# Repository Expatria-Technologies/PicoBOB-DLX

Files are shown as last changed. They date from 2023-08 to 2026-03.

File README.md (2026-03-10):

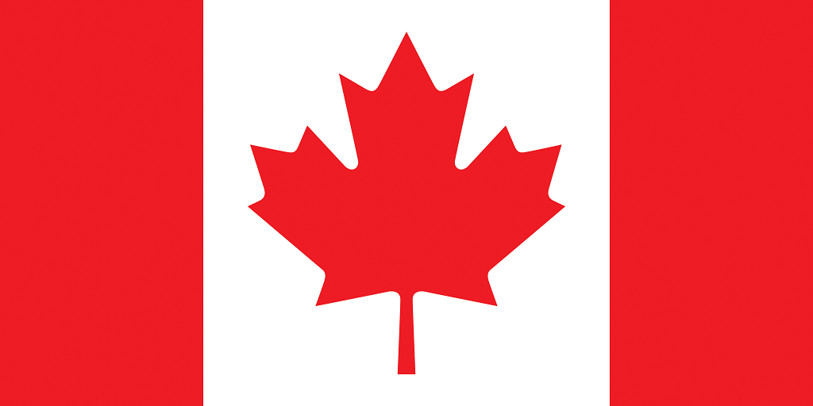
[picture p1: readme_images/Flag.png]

### Canadian-designed open source hardware. For everyone.

# PicoBOB-DLX for GRBLHAL and LinuxCNC

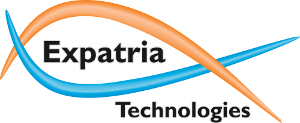
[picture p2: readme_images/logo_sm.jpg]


Expatria Technologies PicoBOB-DLX GRBLHAL/LinuxCNC module

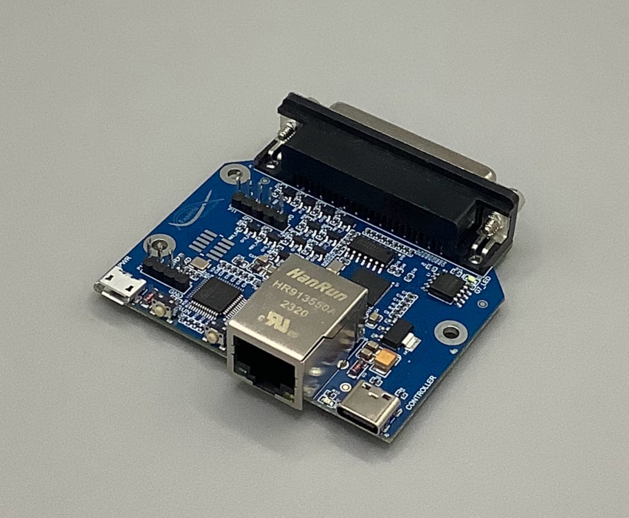
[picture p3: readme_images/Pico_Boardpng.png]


Currently available in our online store:

[https://expatria.myshopify.com/products/picobob-dlx](https://expatria.myshopify.com/products/picobob-dlx)

Please consider buying a board to support our open-source designs. 

An extended version of the original PicoBOB, the PicoBOB-DLX allows you to use either the MCU/Sender based GRBLHAL motion control system, or else it can act as a hardware step generator when connected to a LinuxCNC system over Ethernet.  It is intended to be simple and low cost.  It uses a Raspberry Pi RP2040 MCU and the widely available 5 axis Mach3 breakout board.  It can also be used with the Gecko G540 as well as other devices that use a DB25 parallel port interface.  The complete BOM and fabrications files are in the CAM_OUTPUTS folder for upload.  The design is free to use by all parties, including commercial parties, under the CERN-OHL-S V2 license.  It is our hope that the community finds the design useful and that it may be carried forward to help advance the PrintNC and broader CNC hobby community.

The PicoBOB-DLX closely tracks the features of the Mach3/LinuxCNC BOB:

1) Up to 5 axes of step/direction control.
3) 10A Spindle relay control.
4) 0-10V analog spindle speed control.
5) 5 general purpose inputs
6) One general purpose output.

In addition, it has headers for the Expatria Jog2K real-time control pendant: 

https://github.com/Expatria-Technologies/RT_Jog_Controller

The DLX can be connected to a GRBLHAL host via Ethernet or USBC.  For LinuxCNC, the Ethernet connection is used with the Remora etherent component and the DLX acts as a hardware step generator to mitigate latency demands.

The current work-in-progress version of the Remora RP2040-W5500 firmware is posted here:  
https://github.com/Expatria-Technologies/Remora-RP2040-W5500

The most current version of the GRBLHAL RP2040 driver is posted here:  
https://github.com/Expatria-Technologies/RP2040

The default GRBLHAL builds for the PicoBOB include the following features that are implemented in the RP2040 port of GRBLHAL:

1) Backlash Compensation.
2) Stress-free Autosquaring for the ganged axis
3) Ganged axis offsets to correct for offset homing switches
4) Step rates tested up to 180 KHz on 5 simultaneous axes.

In addition, the board has a USB micro connector for the 5V that is required for the BOB.  There are also pushbuttons for BOOT and RUN for easy programming using the RP2040's built-in UF2 bootloader.

## PicoBOB Overview

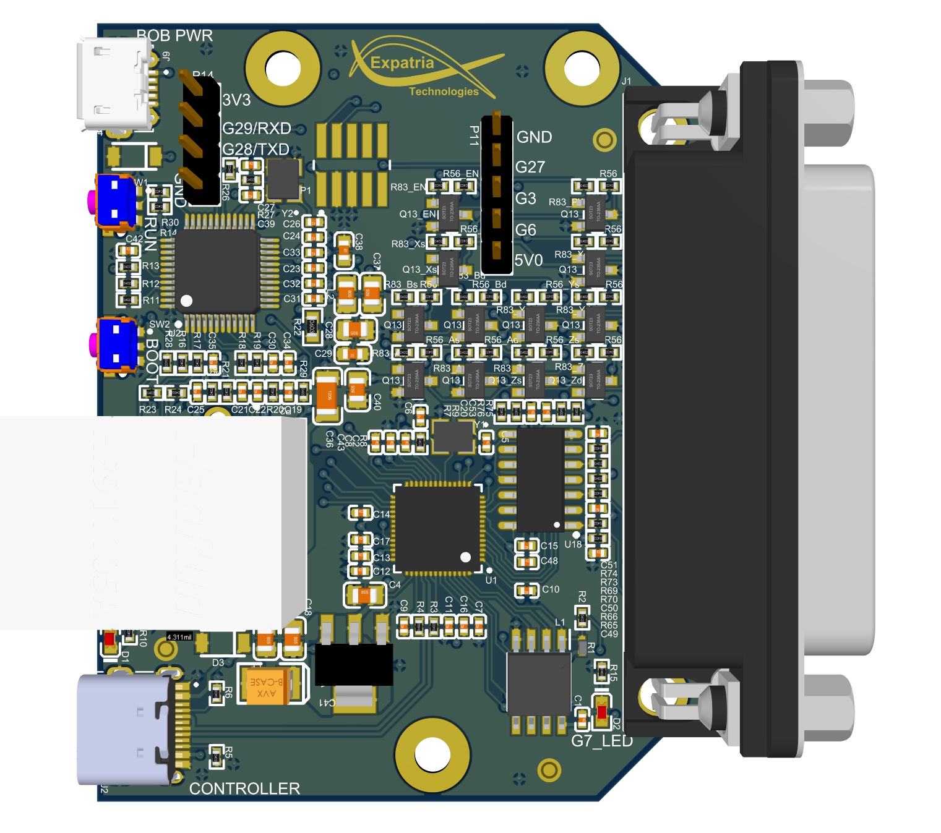
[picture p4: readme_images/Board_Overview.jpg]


Usage notes:

Communication with GRBLHAL is accomplished via the USBC or Ethernet connections on the PicoBOB (not connected in above images).  A short USB cable is used to provide the required 5V for the BOB.  In addition, the BOB requires an external 12-24V supply.

The Mach3 BOB shares the B axis direction signal with a spindle relay enable signal - only one can be used at a time.  Also on the PicoBOB, the stepper enable signal is modified in the GRBLHAL default map file so that it is used as the coolant output signal.  All of this is configurable by re-building the GRBLHAL firwmare.  In linuxcnc, the configuration is uploaded via tftp.

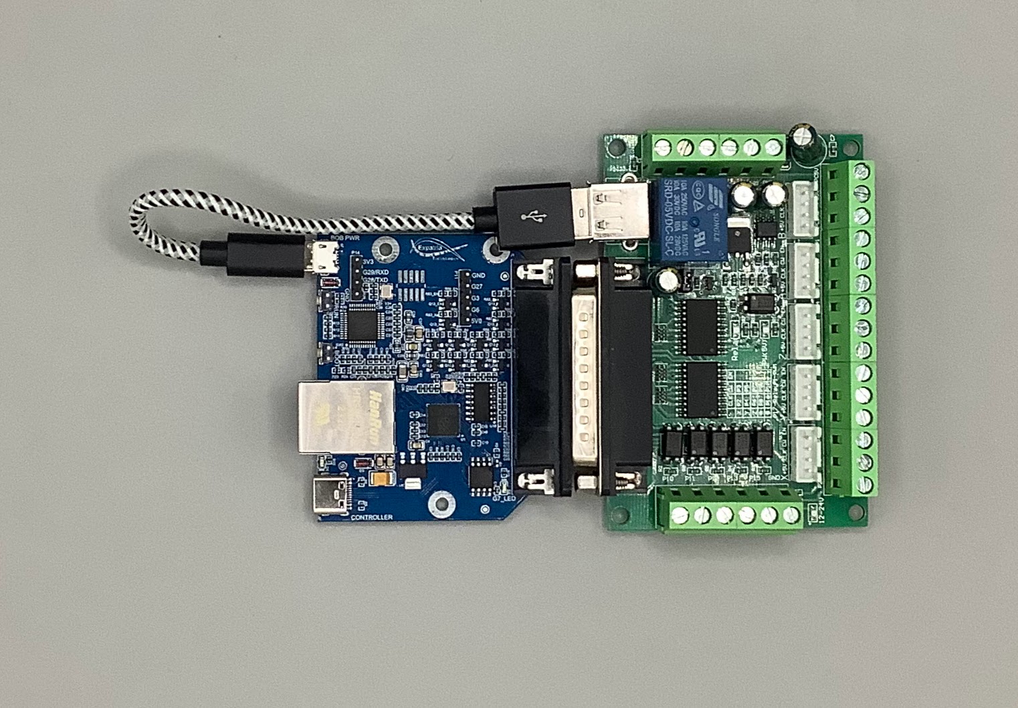
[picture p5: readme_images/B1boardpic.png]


Above shows the PicoBOB B1 connected to the Mach3/LinuxCNC parallel BOB.

YGANG pinout is as below:

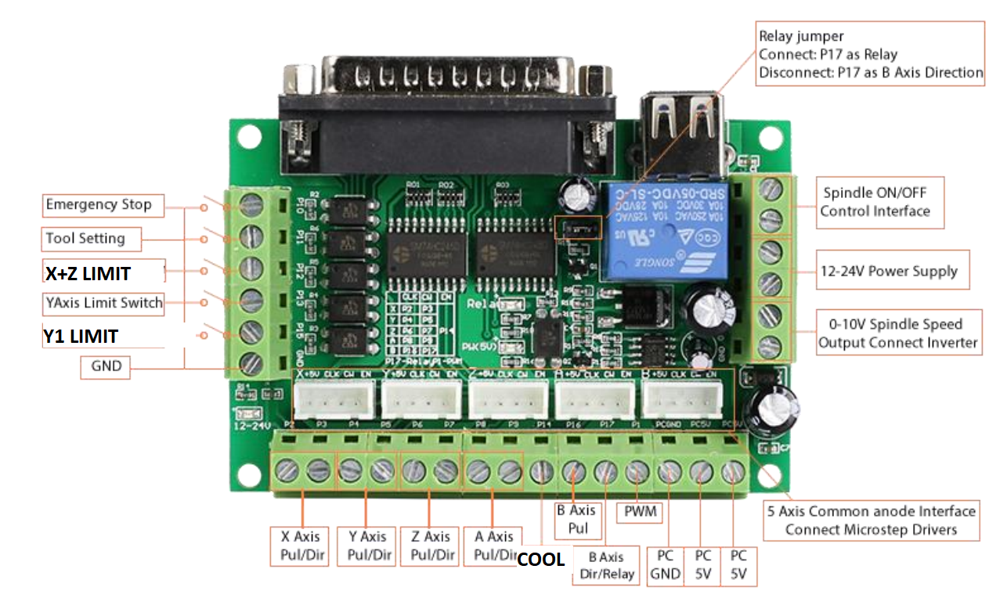
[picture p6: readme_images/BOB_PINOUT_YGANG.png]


## Gecko Drive G540 support Overview
By using a common "mini gender changer" the PicoBOB DLX can be adapted for use with a G540 4-AXIS Digital Step Drive.

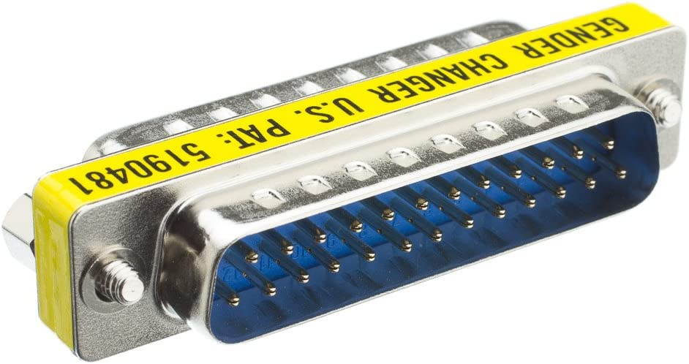
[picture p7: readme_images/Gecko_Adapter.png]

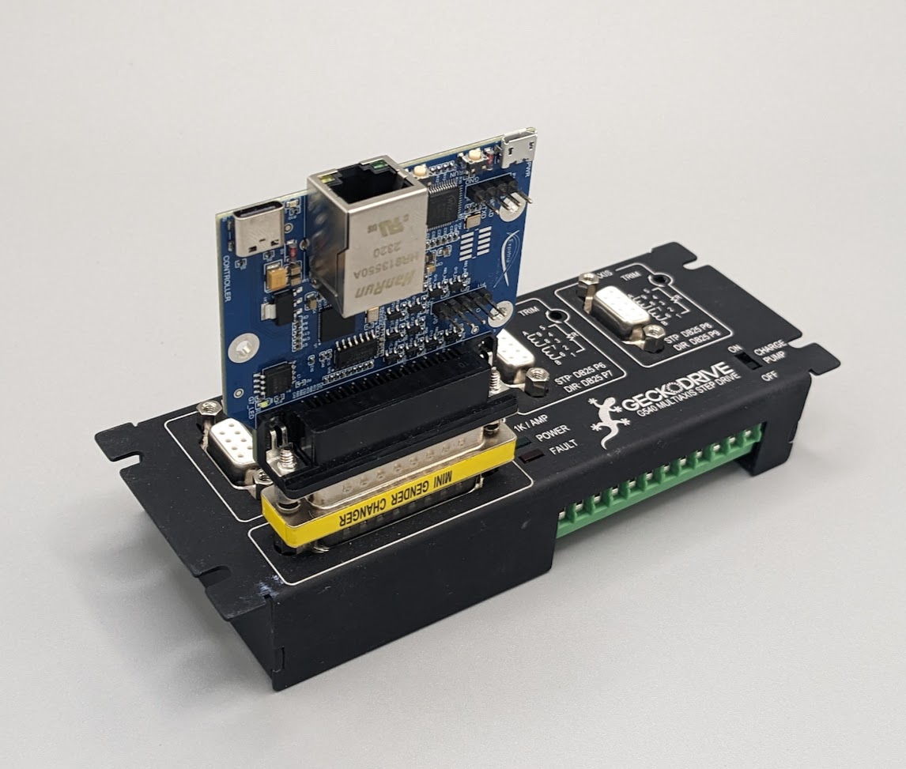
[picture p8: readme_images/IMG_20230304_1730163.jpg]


The updated GRBLHAL map file has the following pinout:

| DB25 Pin | G540 Function | GRBLHAL Function | RP2040 GPIO |
|---|---|---|---|
| Pin 1 | OUTPUT 2 | SPINDLE ENABLE | GPIO14 |
| Pin 2 | X STEP | X STEP | GPIO17 |
| Pin 3 | X DIR | X DIR | GPIO9 |
| Pin 4 | Y SETP | Y SETP | GPIO18 |
| Pin 5 | Y DIR | Y DIR | GPIO10 |
| Pin 6 | Z STEP | Z STEP | GPIO19 |
| Pin 7 | Z DIR | Z DIR | GPIO11 |
| Pin 8 | A STEP | A/M3 STEP | GPIO20 |
| Pin 9 | A DIR | A/M3 DIR | GPIO12 |
| Pin 10 | INPUT 1 | LIMIT XYZ | GPIO3 |
| Pin 11 | INPUT 2 | PROBE | GPIO4 |
| Pin 12 | INPUT 3 | LIMIT A/M3 | GPIO2 |
| Pin 13 | INPUT 4 | HOLD | GPIO1 |
| Pin 14 | VFD PWM | SPINDLE PWM | GPIO16 |
| Pin 15 | FAULT (INPUT 5) | HALT | GPIO5 |
| Pin 16 | CHARGE PUMP | N/A | GPIO21 |
| Pin 17 | OUTPUT 1 | COOLANT | GPIO13 |
| Pin 18-25| GND | | |

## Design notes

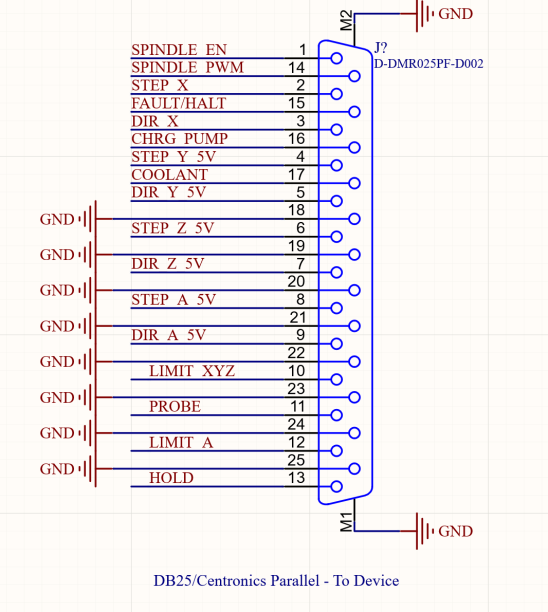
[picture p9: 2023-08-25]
readme_images/g540_pinout.png

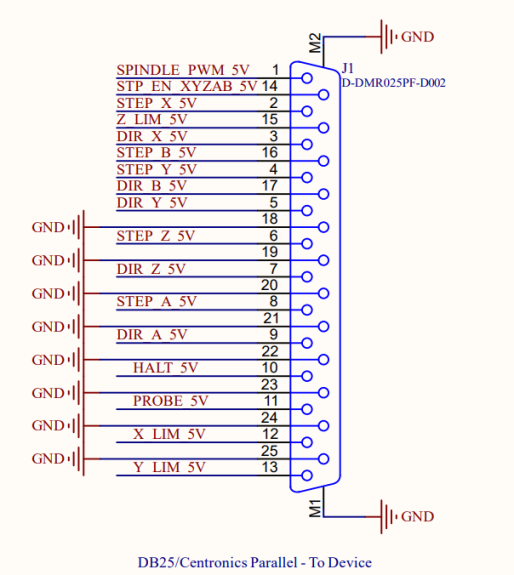
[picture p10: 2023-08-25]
readme_images/picoBOB_Pinout.png

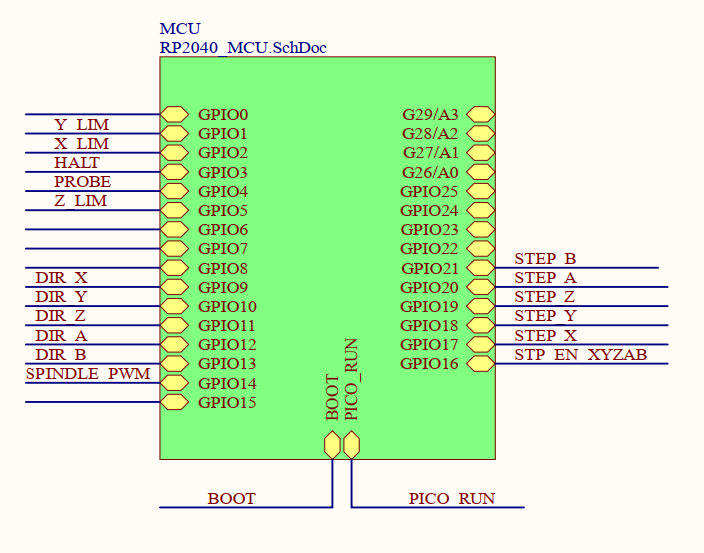
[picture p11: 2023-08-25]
readme_images/default_pinout.png

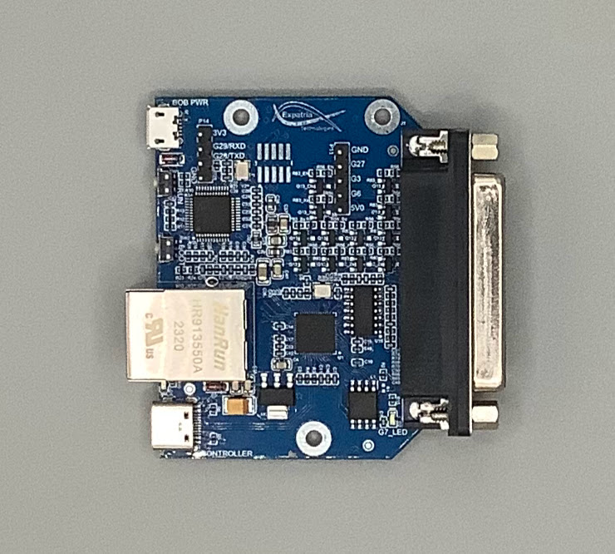
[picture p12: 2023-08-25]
readme_images/Pico_Top.png

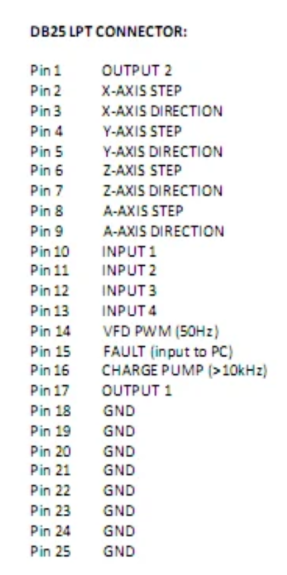
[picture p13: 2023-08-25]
readme_images/G540_DB25_ref.png

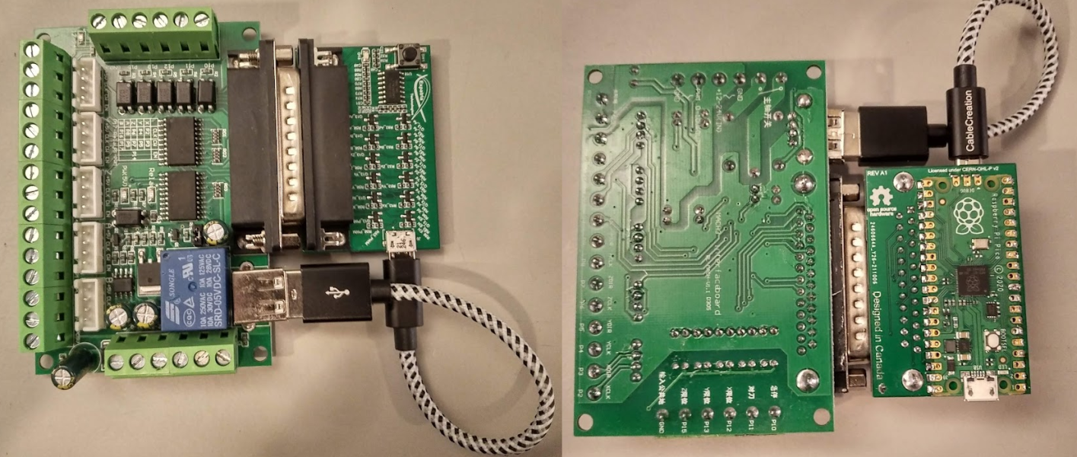
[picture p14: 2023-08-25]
readme_images/boardpics.png

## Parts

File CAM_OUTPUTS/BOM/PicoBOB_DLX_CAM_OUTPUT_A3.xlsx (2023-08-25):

Comment | Description | Designator | Footprint | SuppliersPartNumber | Quantity
100nF | Chip capacitors | C1, C7, C8, C11, C12, C13, C14, C15, C16, C17, C30, C31, C32, C33, C34, C35, C39 | 0402_C | C1525 | 17
4.7uF | Chip capacitor | C2, C23 | 0402_C | C23733 | 2
22uF | Chip capacitors | C3, C4, C18, C28, C37, C40 | 0805_C | C2922481 | 6
10pF | Chip capacitors | C5, C6, C26, C27 | 0402_C | C32949 | 4
1.0uF | Chip capacitor | C9, C10, C42, C43, C48 | 0402_C | C52923 | 5
10nF | Chip capacitors | C19, C20, C24, C49, C50, C51, C53 | 0402_C | C15195 | 7
6.8nF | Chip capacitors | C21, C22 | 0402_C | C1542 | 2
22nF | Chip capacitors | C25 | 0402_C | C1532 | 1
4.7uF | Chip capacitors | C29, C38 | 0603_C | C19666 | 2
1nF | Chip capacitors | C36 | 1206_C | C35216 | 1
100uF | Tantalum capacitor | C41 | CASE-B_3528 | C16133 | 1
0603 Green | LED | D1 | 0603_LED_S1 | C72043 | 1
0603 White | LED | D2 | 0603_LED_S1 | C2290 | 1
ZMM5V6 | 500mW - 0.1uA @ 1V 5.6V LL-34 Zener Diodes ROHS | D3, D4 | LL-34 | C8062 | 2
D-DMR025PF-D002 | Through Hole,P=2.77mm D-Sub Connectors ROHS | J1 | 618025231121 | C190083 | 1
TYPE-C-31-M-12 | USB Connectors 24 Receptacle 1 8.94*7.3mm RoHS | J2 | HRO_TYPE-C-31-M-12 | C165948 | 1
MICROXNJ | Micro USB | J9 | SHOUHAN_MICROXNJ | C404969 | 1
W25Q128JVSIQ_TR | Inductor | L1 | SOIC127P780X195-8N | C97521 | 1
220Ω @ 100MHz 1 2A | 220Ω @ 100MHz 1 2A 150mΩ 0805 Ferrite Beads ROHS | L2 | 0805_C | C139188 | 1
Magjack | HR911105A Ethernet Interface Arduino Platform Evaluation Expansion Board | P2 | HANRUN_HR911105A | C163507 | 1
Header 5 | Header, 5-Pin | P11 | HDR1X5 | C124379 | 1
Header 4 | Header, 4-Pin | P14 | HDR1X4 | C124378 | 1
MMBT5551 G1 | 三极管 | Q13_Ad, Q13_As, Q13_Bd, Q13_Bs, Q13_EN, Q13_PWM, Q13_Xd, Q13_Xs, Q13_Yd, Q13_Ys, Q13_Zd, Q13_Zs | SOT-23(SOT-23-3) | C2145 | 12
DNP | Resistor, ±5%, 0.05W | R1 | 0402 |  | 1
1KΩ ±1% | Chip resistor | R2 | 0402_R | C11702 | 1
22Ω ±1% | Chip resistor | R3, R4 | 0402_R | C25092 | 2
5.1KΩ ±1% | Chip resistor | R5, R6, R10 | 0402_R | C25905 | 3
100KΩ ±1% | Chip resistor | R7, R65, R69, R73, R75 | 0402_R | C25741 | 5
470Ω ±1% | Chip resistor | R8 | 0402_R | C25117 | 1
510Ω ±1% | Chip resistor | R9, R15, R66, R70, R74, R76 | 0402_R | C25123 | 6
10KΩ ±1% | Chip resistor | R11, R12, R13, R14 | 0402_R | C25744 | 4
33Ω ±1% | Chip resistor | R16, R17, R18, R19 | 0402_R | C25105 | 4
49.9Ω ±1% | Chip resistor | R20, R21, R23, R24 | 0402_R | C25120 | 4
12.4KΩ ±1% | Chip resistor | R22 | 0603_R | C22865 | 1
10Ω ±1% | Chip resistor | R25 | 0402_R | C25077 | 1
1MΩ ±1% | Chip resistor | R26 | 0402_R | C26083 | 1
0Ω ±1% | Chip resistor | R27 | 0402_R | C17168 | 1
330Ω ±1% | Chip resistor | R28, R29, R56_Ad, R56_As, R56_Bd, R56_Bs, R56_EN, R56_PWM, R56_Xd, R56_Xs, R56_Yd, R56_Ys, R56_Zd, R56_Zs | 0402_R | C25104 | 14
4.7KΩ ±1% | Chip resistor | R30 | 0402_R | C25900 | 1
2.2KΩ ±1% | Chip resistor | R83_Ad, R83_As, R83_Bd, R83_Bs, R83_EN, R83_PWM, R83_Xd, R83_Xs, R83_Yd, R83_Ys, R83_Zd, R83_Zs | 0402_R | C25879 | 12
SKRTLAE010 | Side Push Type, 250 V, -40 to 90 degC, 3-Pin SMD, RoHS, Tape and Reel | SW1, SW2 | ALPS-SKRTLAE010_V | C110293 | 2
RP2040 | RP2040 First MCU from RPI | U1 | RP2040 |  | 1
W5500 | Ethernet Controllers 2.97V ~ 3.63V 10/100 Base-T/TX PHY SPI LQFP-48_7x7x05P Ethernet ICs ROHS | U2 | LQFP-48_7x7x05P | C32843 | 1
74HC14D | 74系列逻辑芯片 | U18 | SOIC-14_150mil | C5605 | 1
AMS1117-3.3 | Vout=3.3V 1A 72dB@(120Hz) (LDO) | VR1 | SOT-223 | C6186 | 1
YSX321SL | Crystal or Oscillator | Y1 | YSX321SL | C9002 | 1
25.0 MHz | Crystal or Oscillator | Y2 | YSX321SL | C13740 | 1

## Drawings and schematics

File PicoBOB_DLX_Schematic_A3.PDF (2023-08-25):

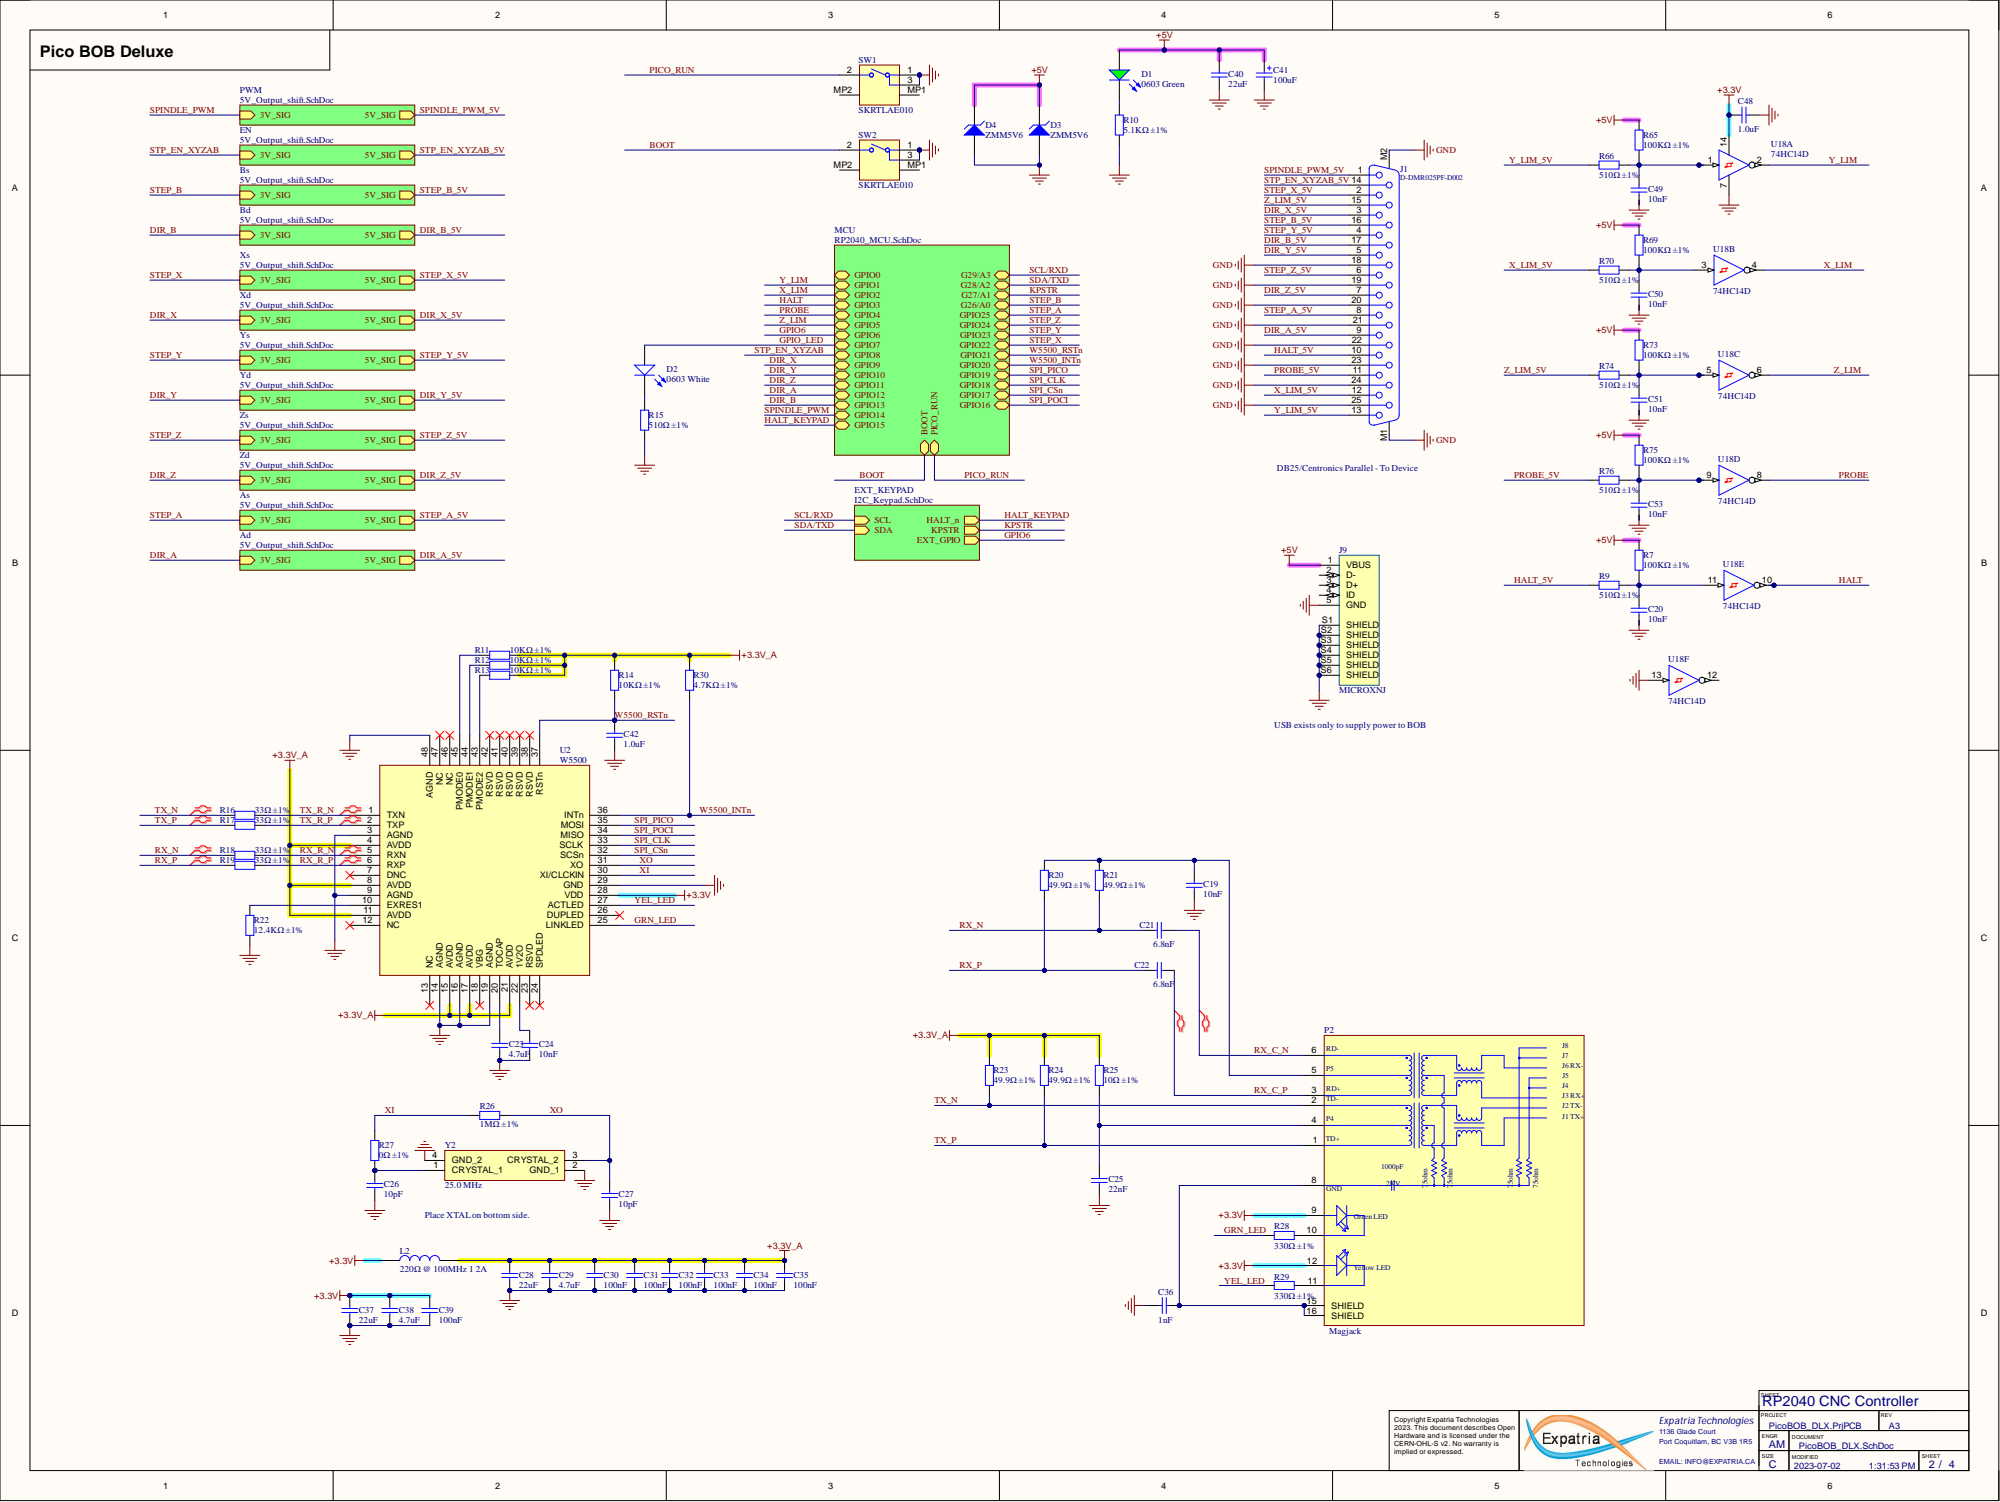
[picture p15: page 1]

R1 | 2 | 1 0 | K Ω ± 1 %
R1 | 3 | 1 0 | K Ω ± 1 %

Hardware a n d i s l i e s d u er th CERN-OHL-S v 2. No warra nty i m p or x pre . | | P OJE PicoBOB_DLX.Prj | R V A3

B Copyright Expatria Technologies 2023. This document describes Open

N G A | C U PicoBOB_DLX.Sc h D o c

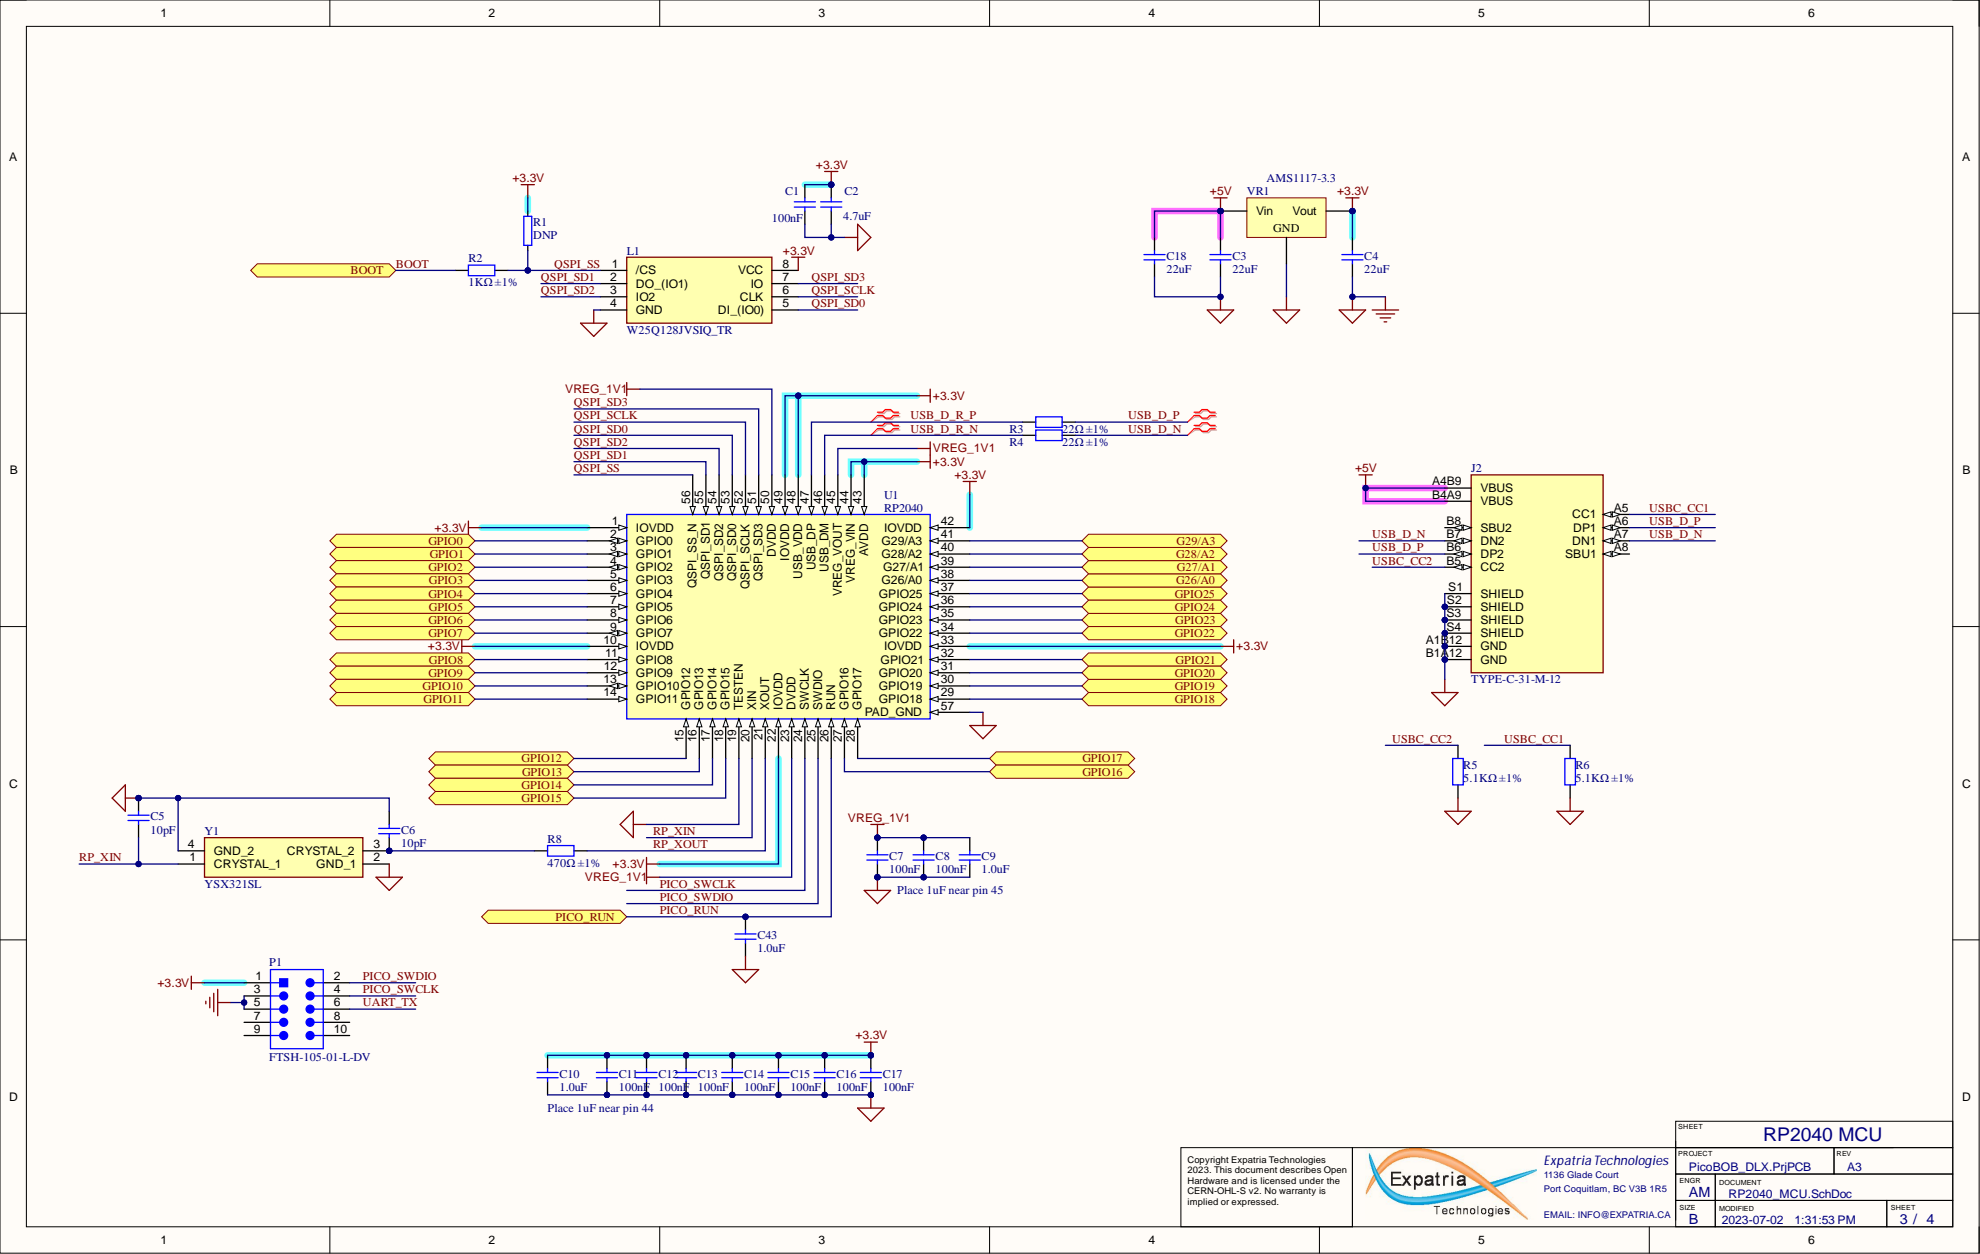
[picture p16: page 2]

QSPI_SD2
QSPI_SD1
QSPI_SS

Copyright Expatria Technologies 2023. This document describes Open Hardware and is licensed under the CERN-OHL-S v2. No warranty is implied or expressed. | | PROJECT PicoBOB_DLX.PrjPCB | REV

ENGR AM | DOCUMENT RP2040_MCU.SchDoc

SIZE B | MODIFIED 2023-07-02 1:31:53 PM | SHEET 3 / 4

EMAIL: INFO@EXPATRIA.CA

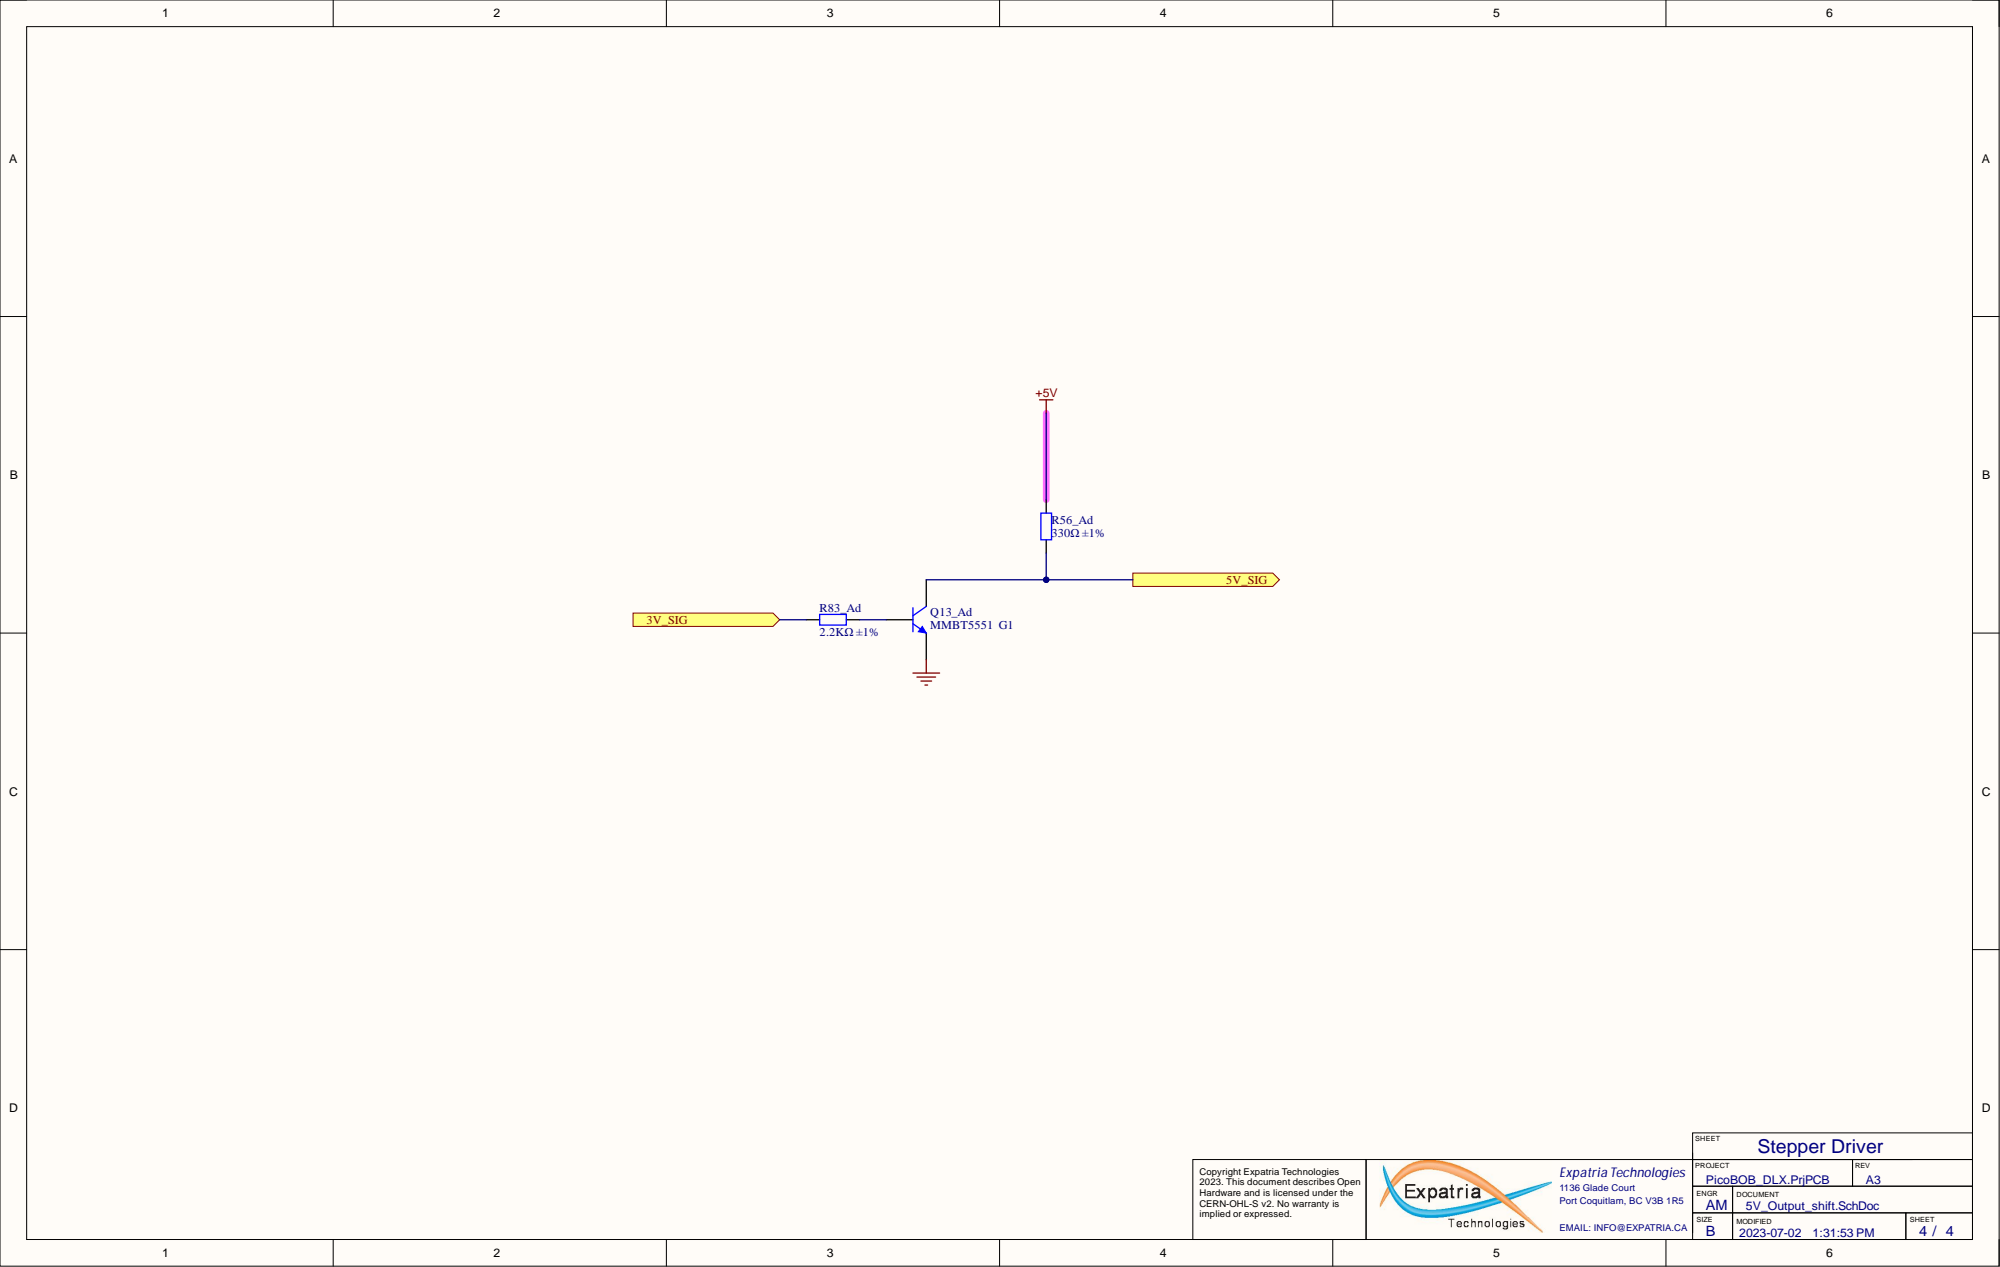
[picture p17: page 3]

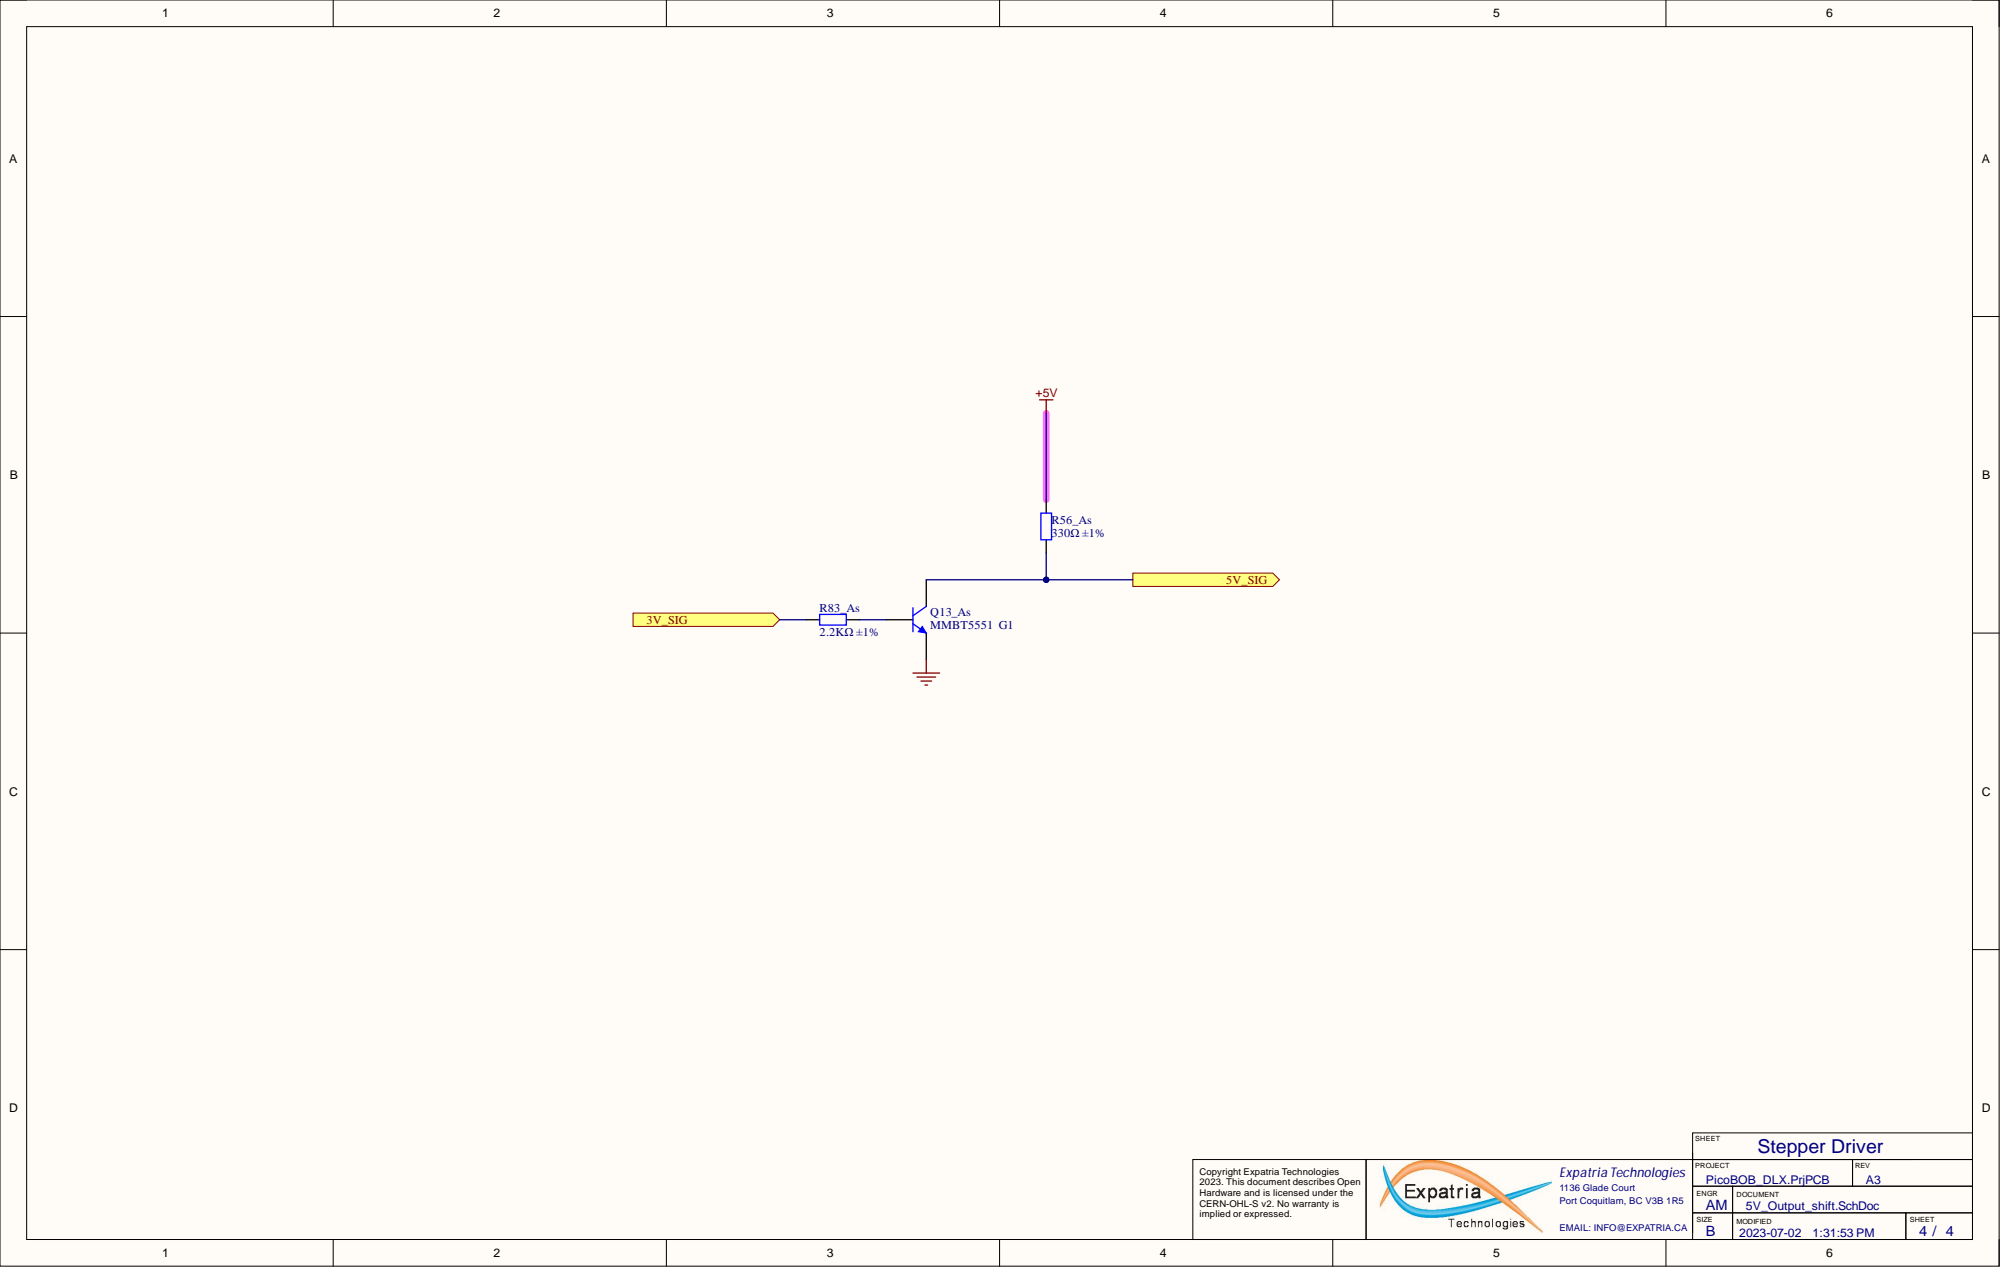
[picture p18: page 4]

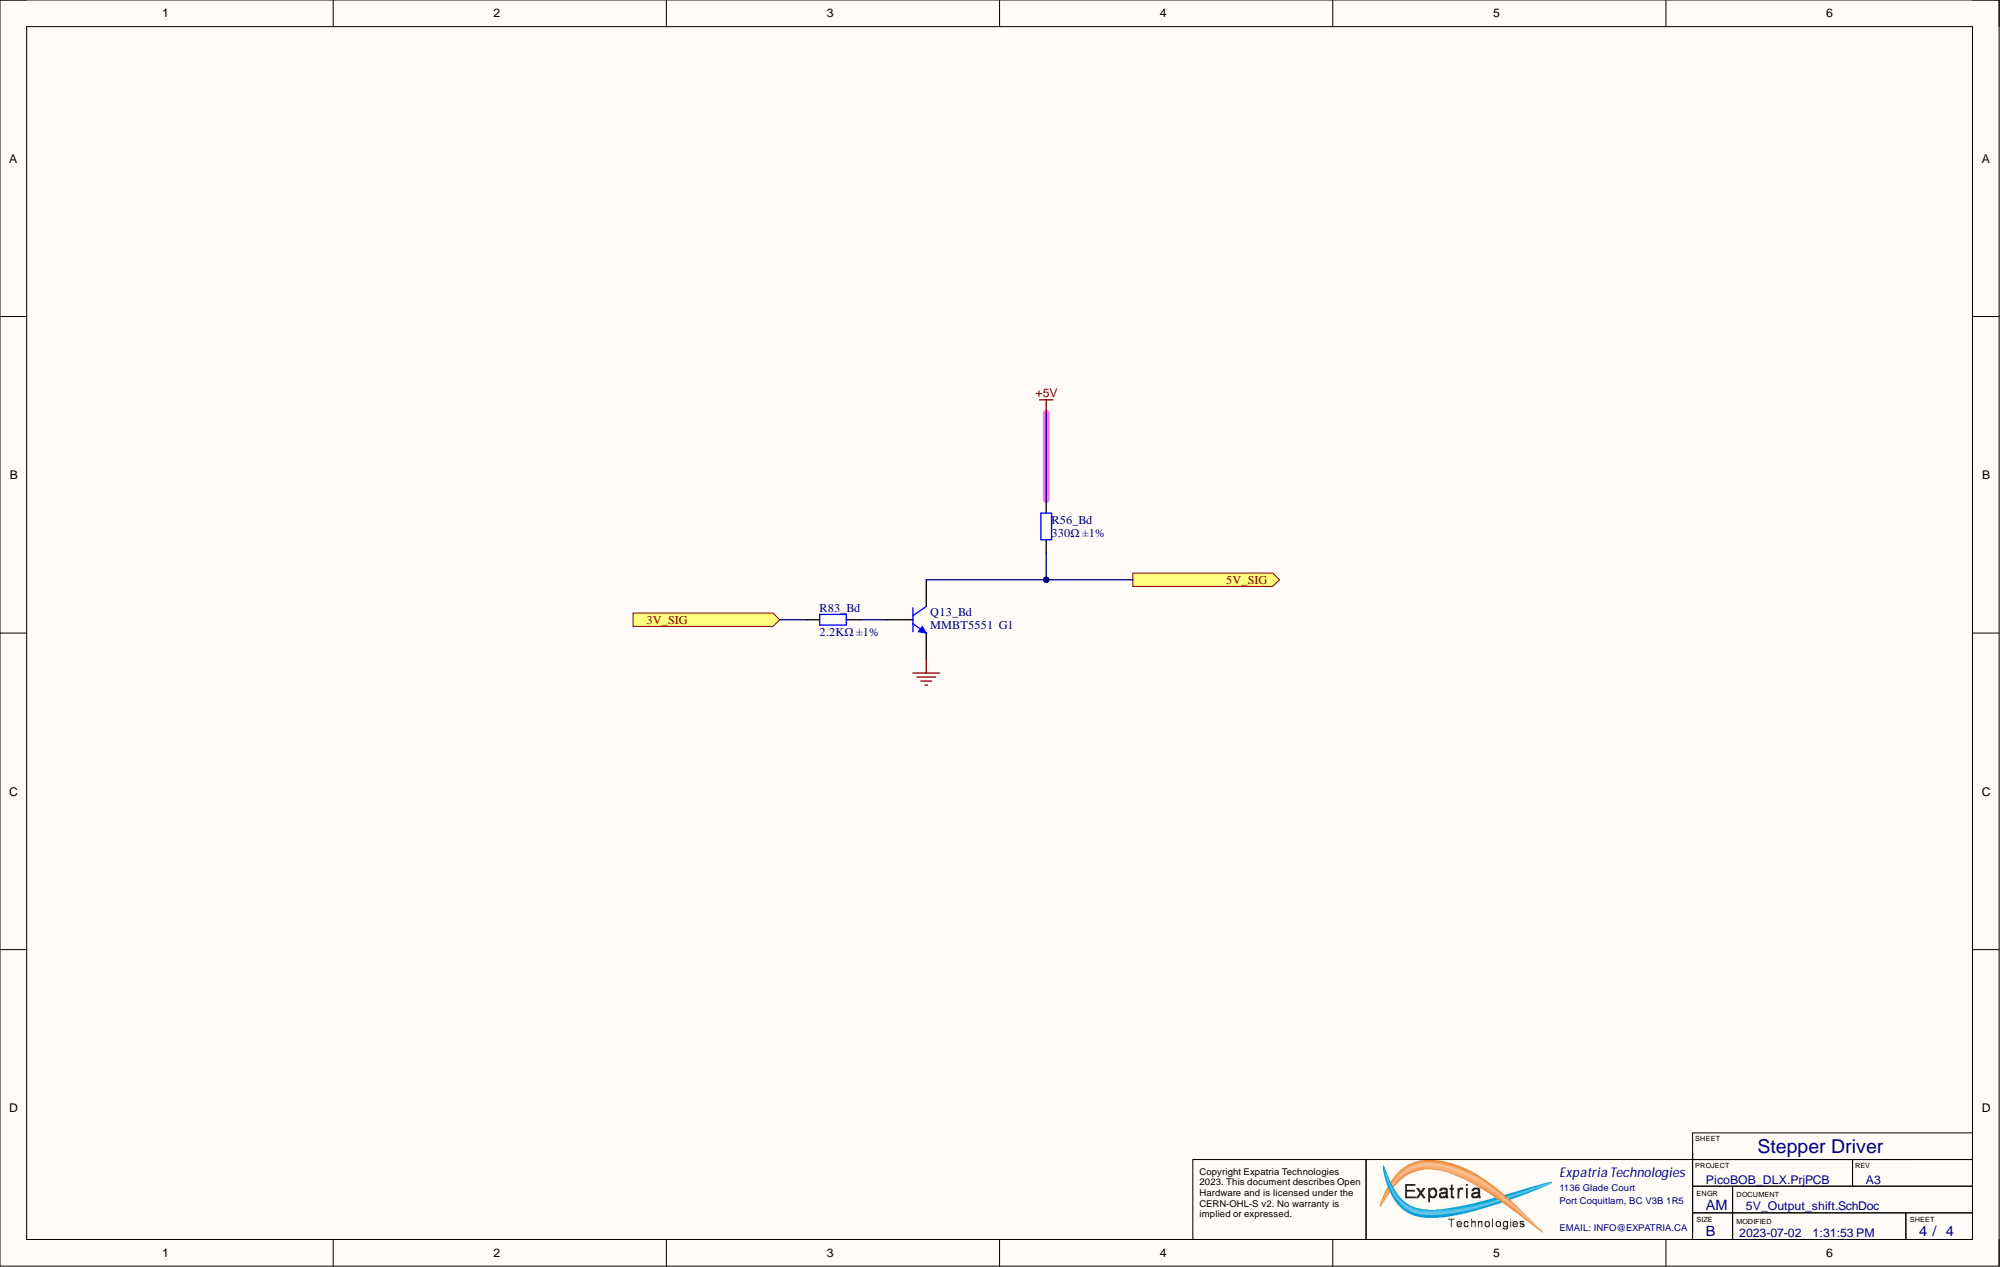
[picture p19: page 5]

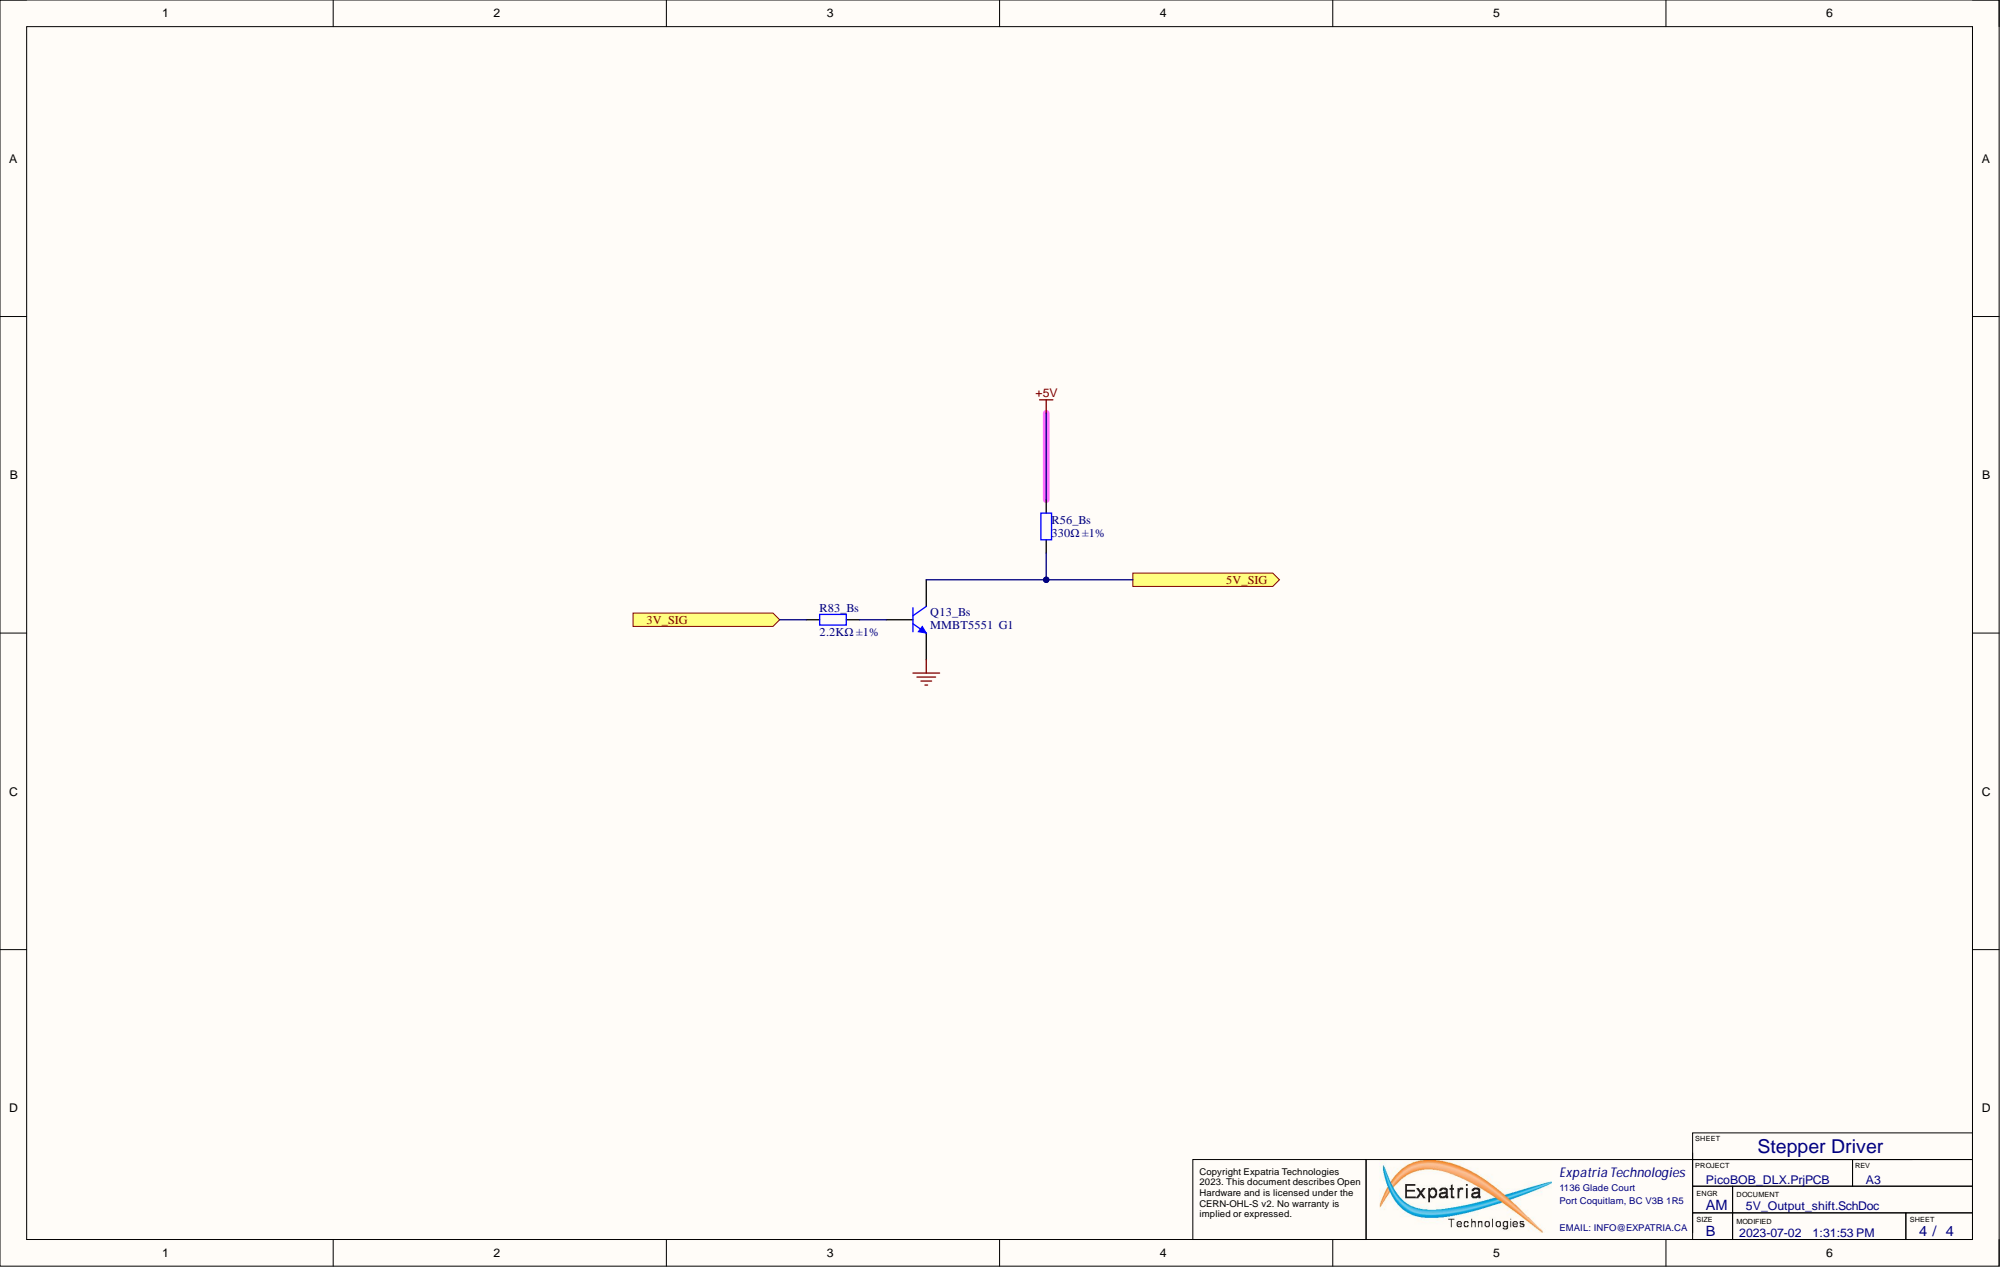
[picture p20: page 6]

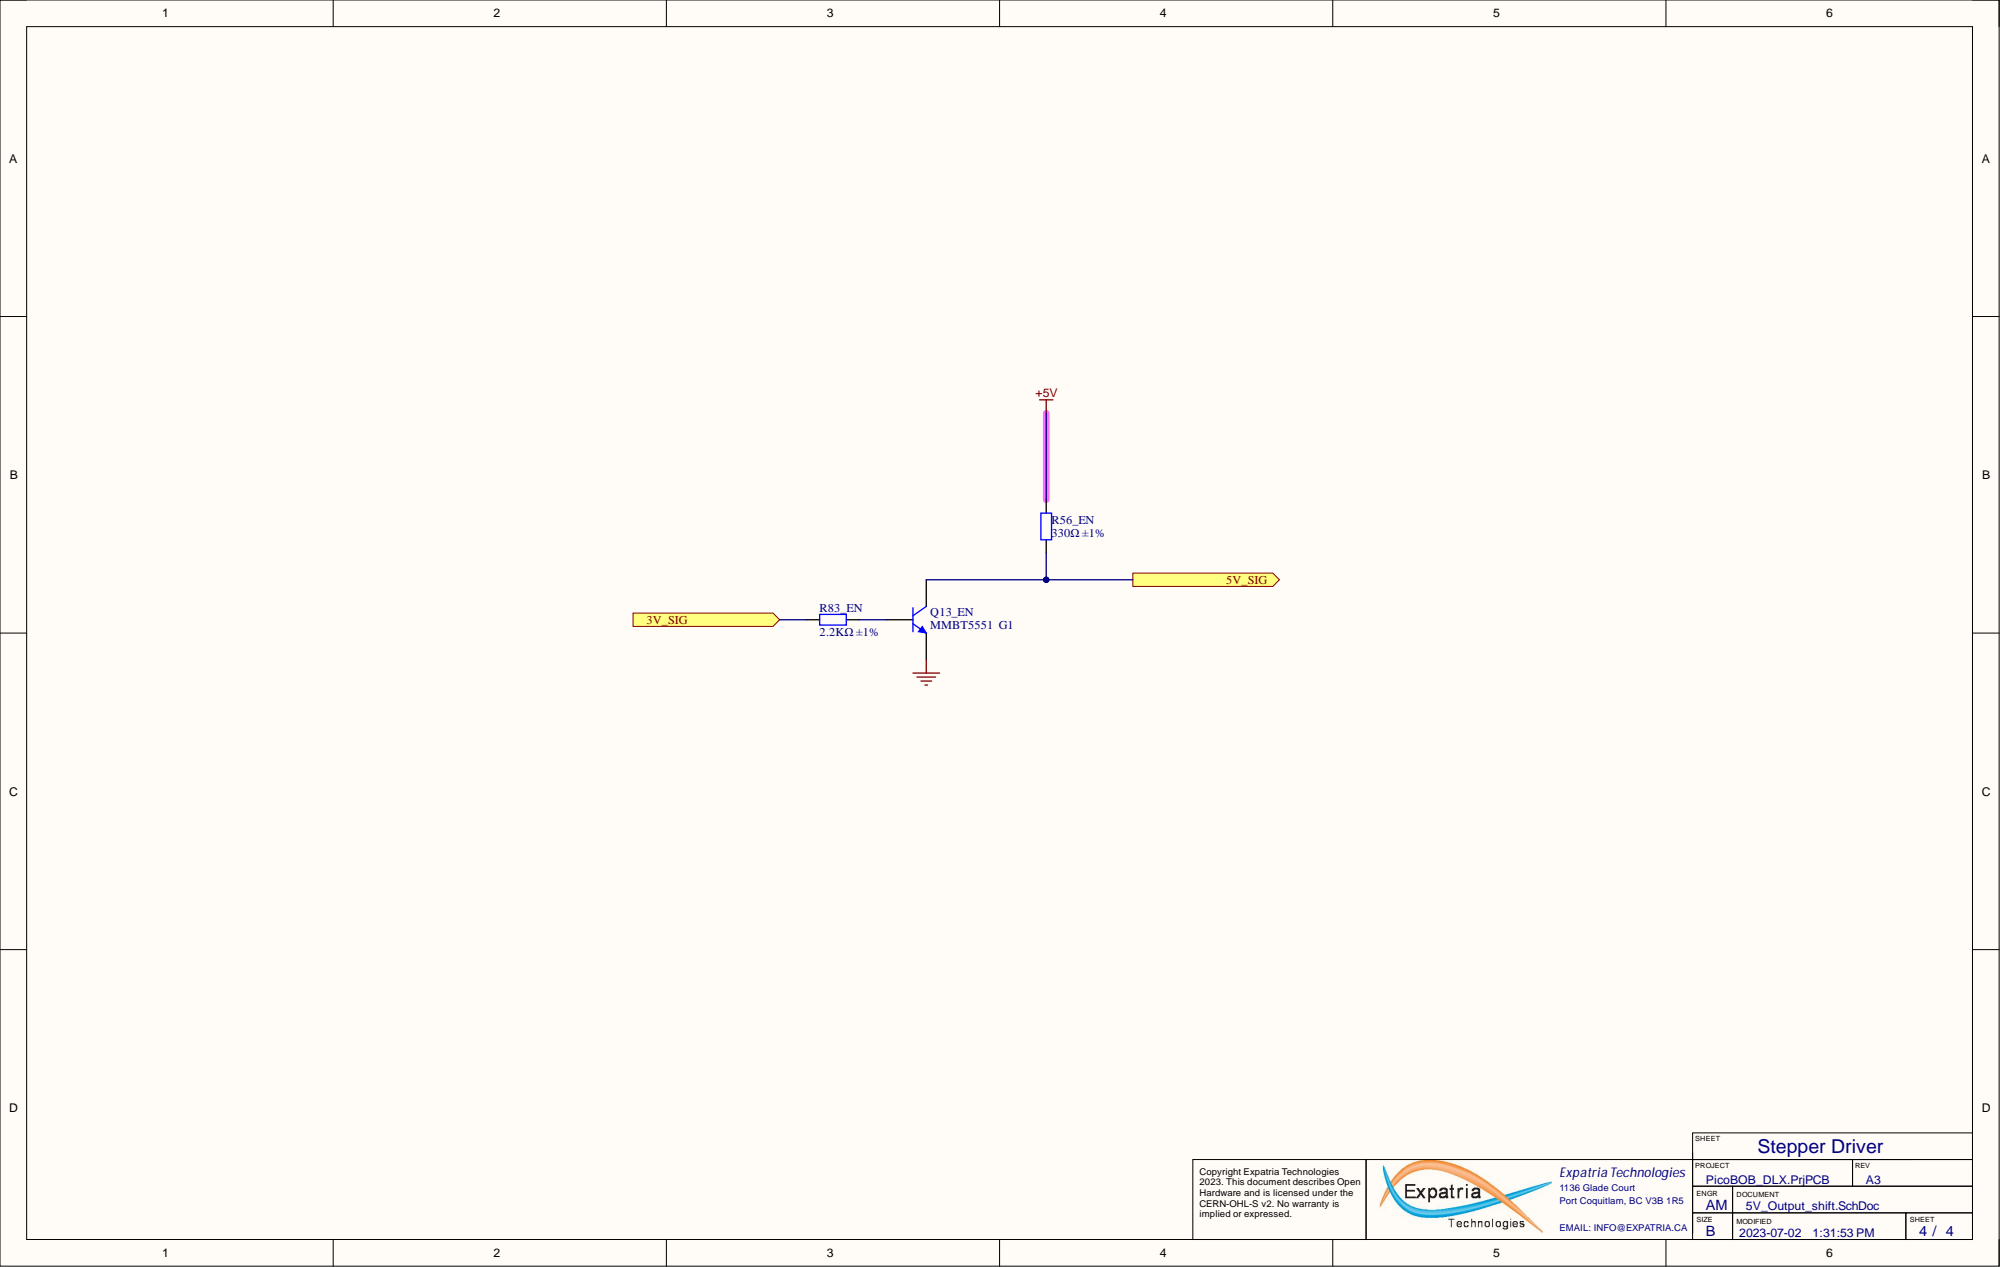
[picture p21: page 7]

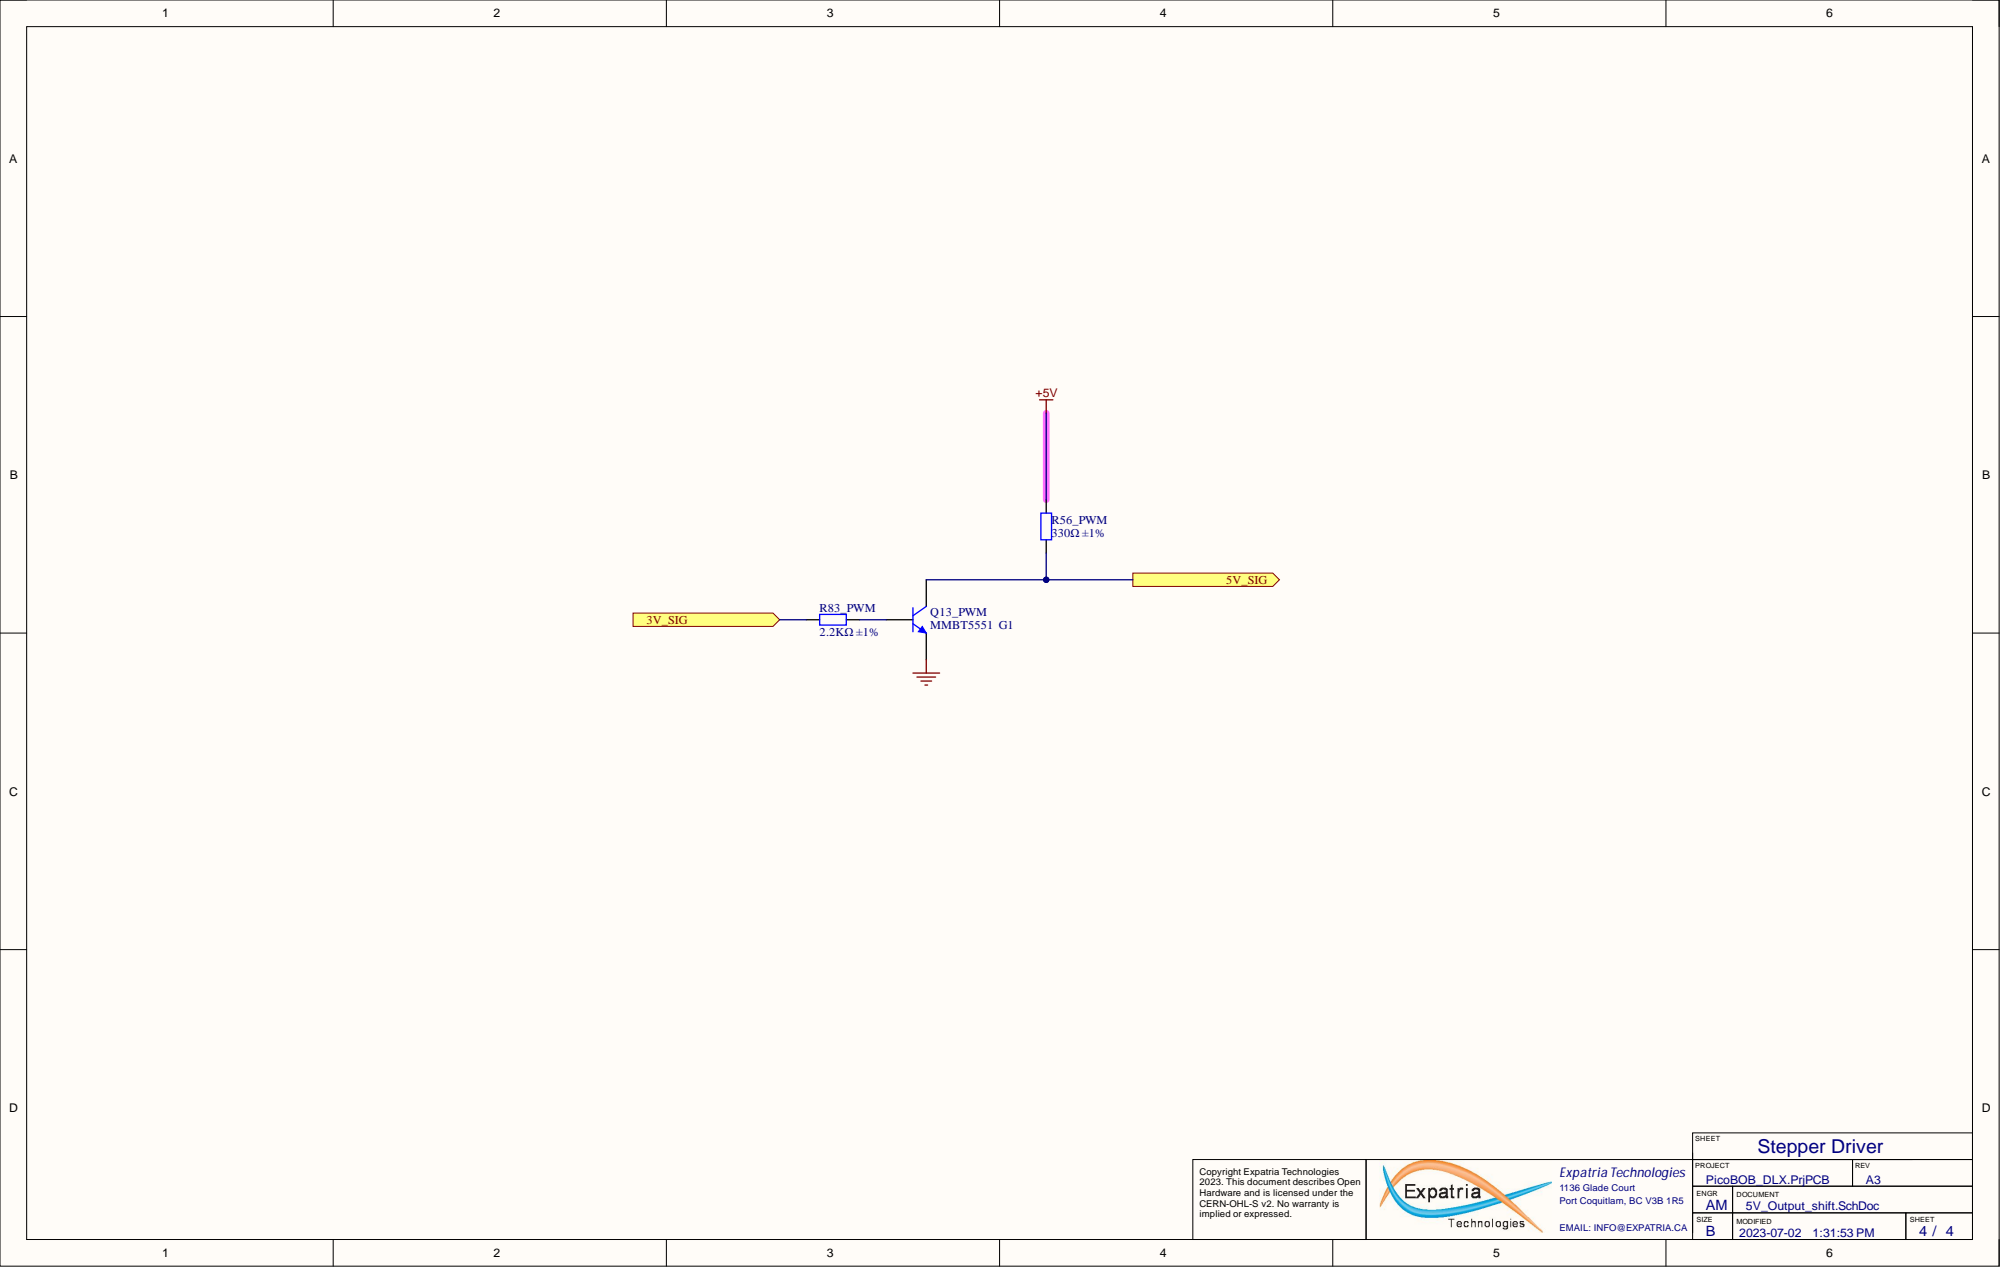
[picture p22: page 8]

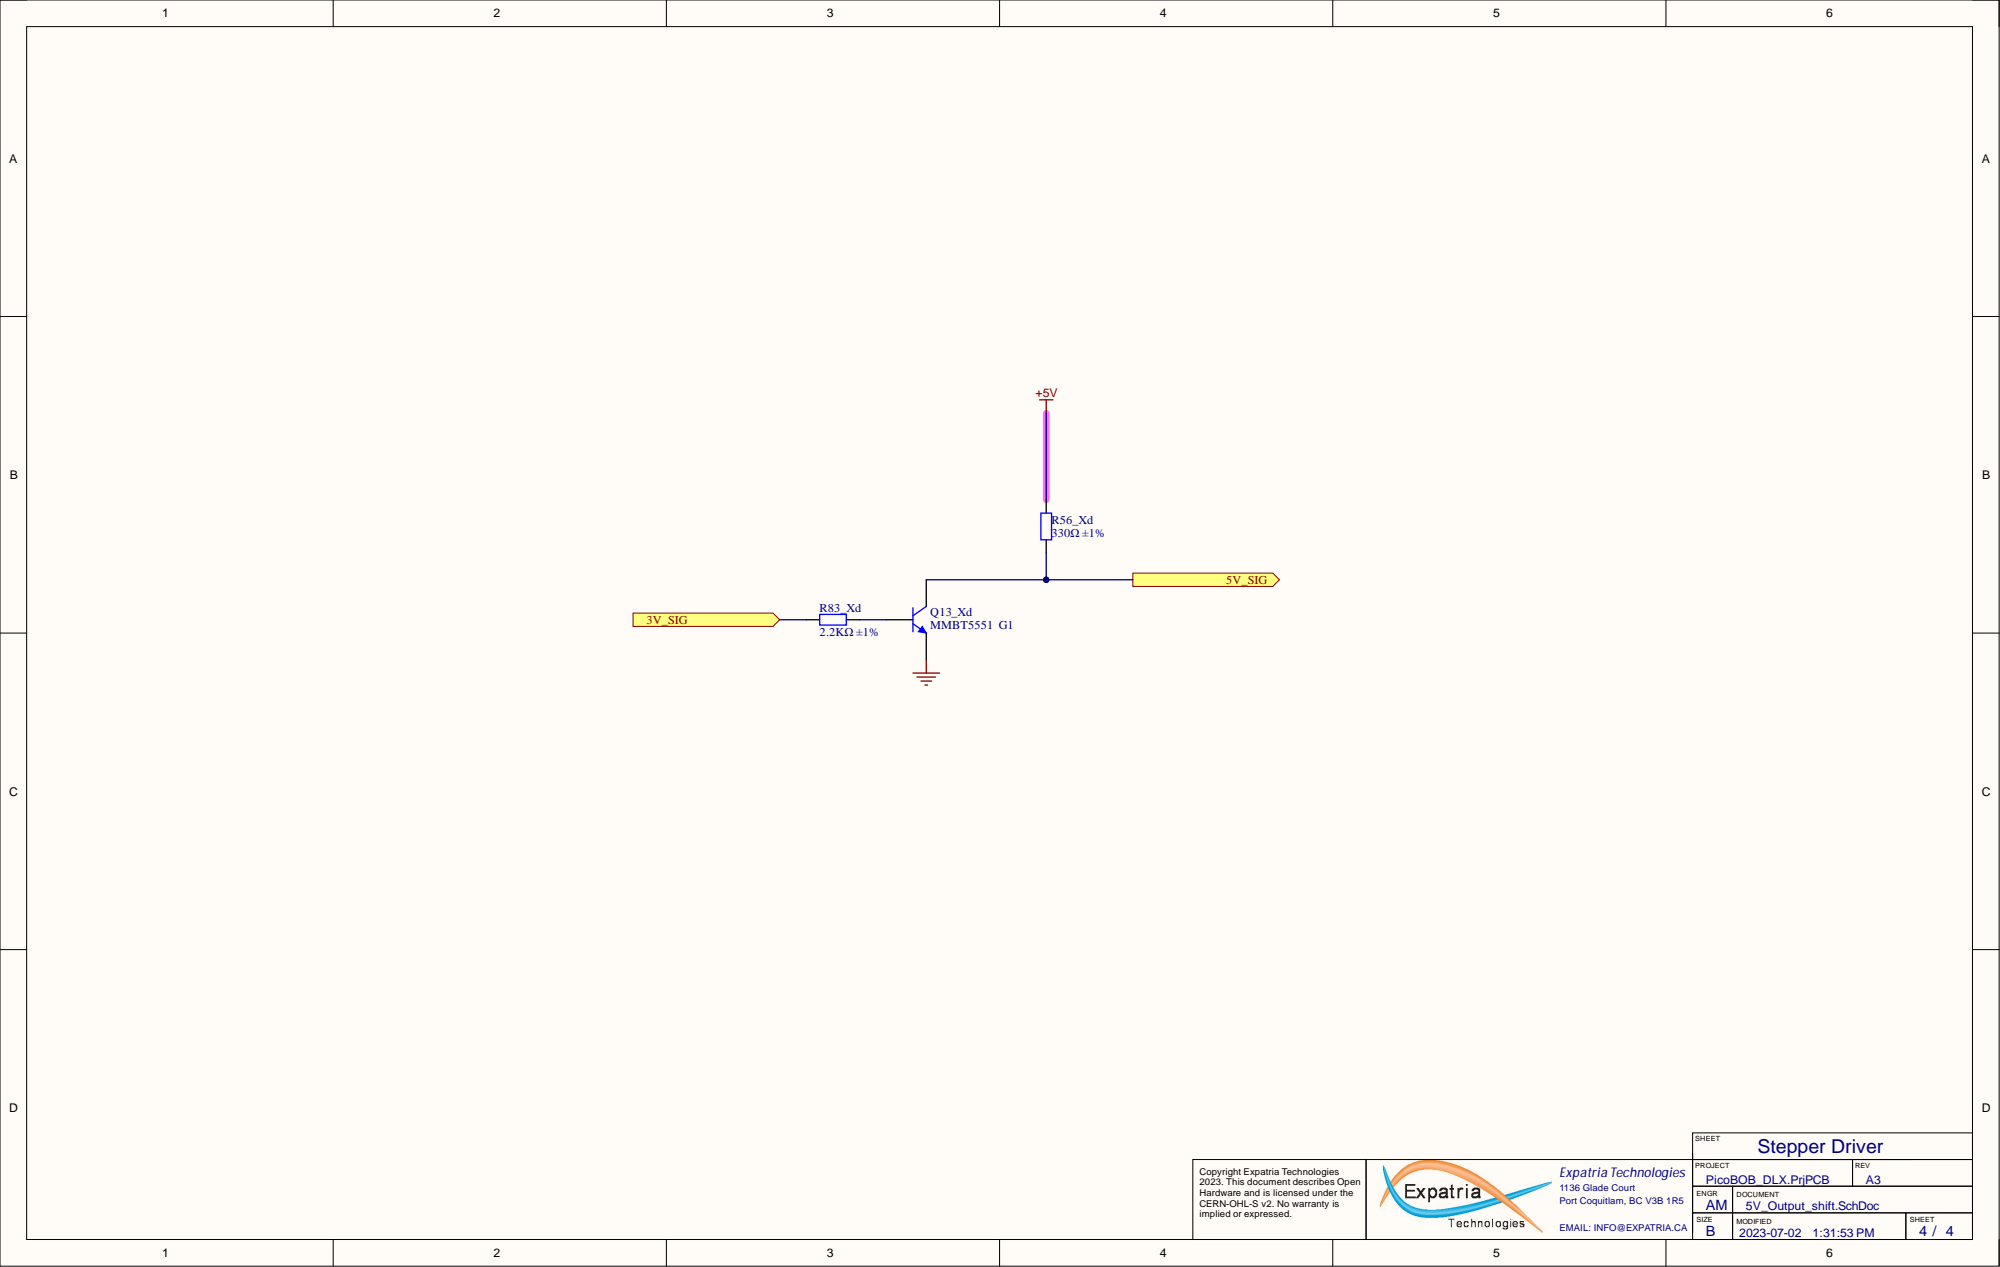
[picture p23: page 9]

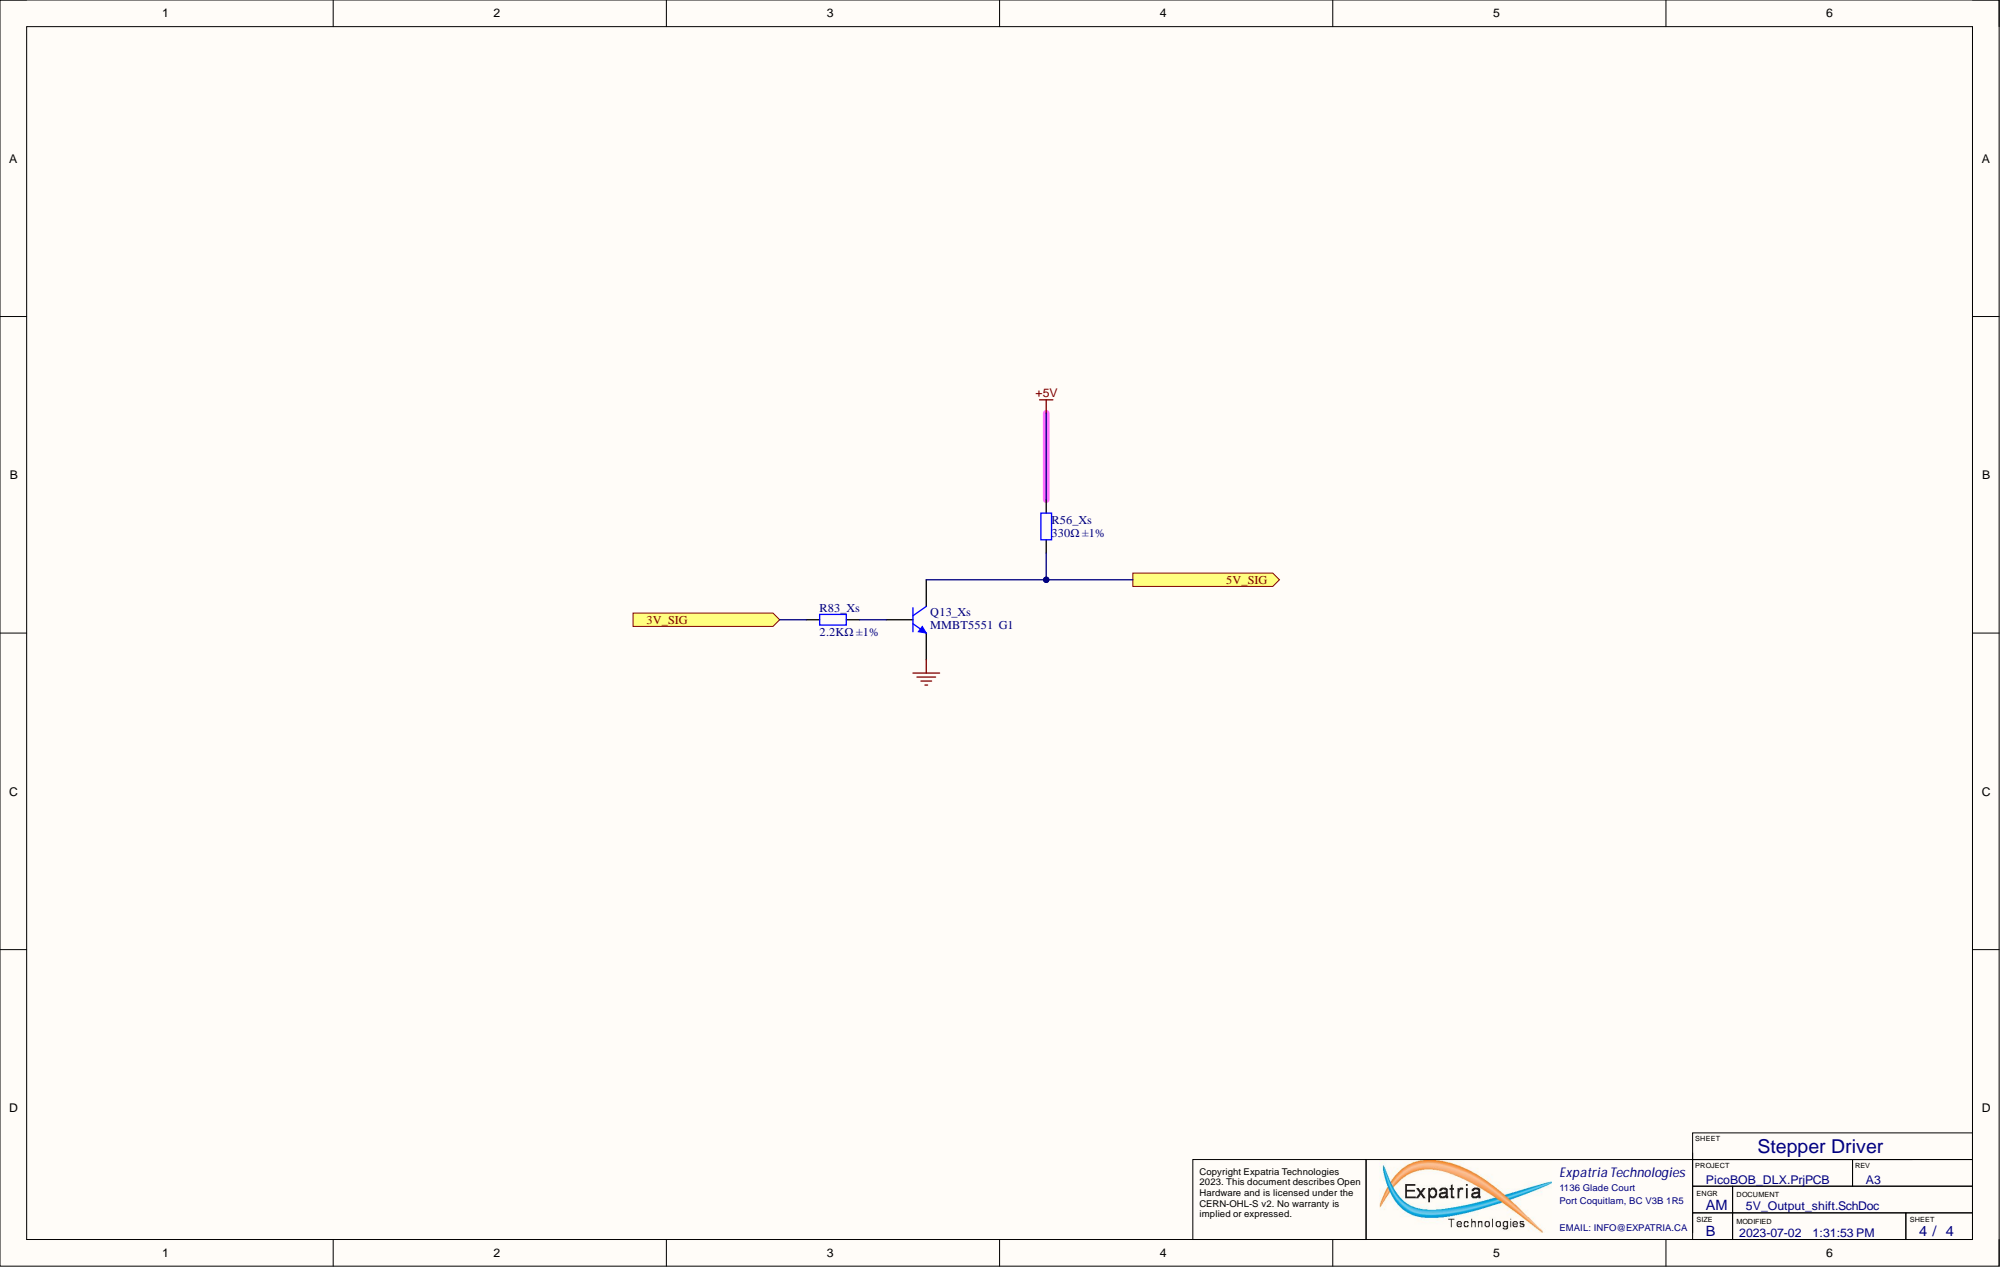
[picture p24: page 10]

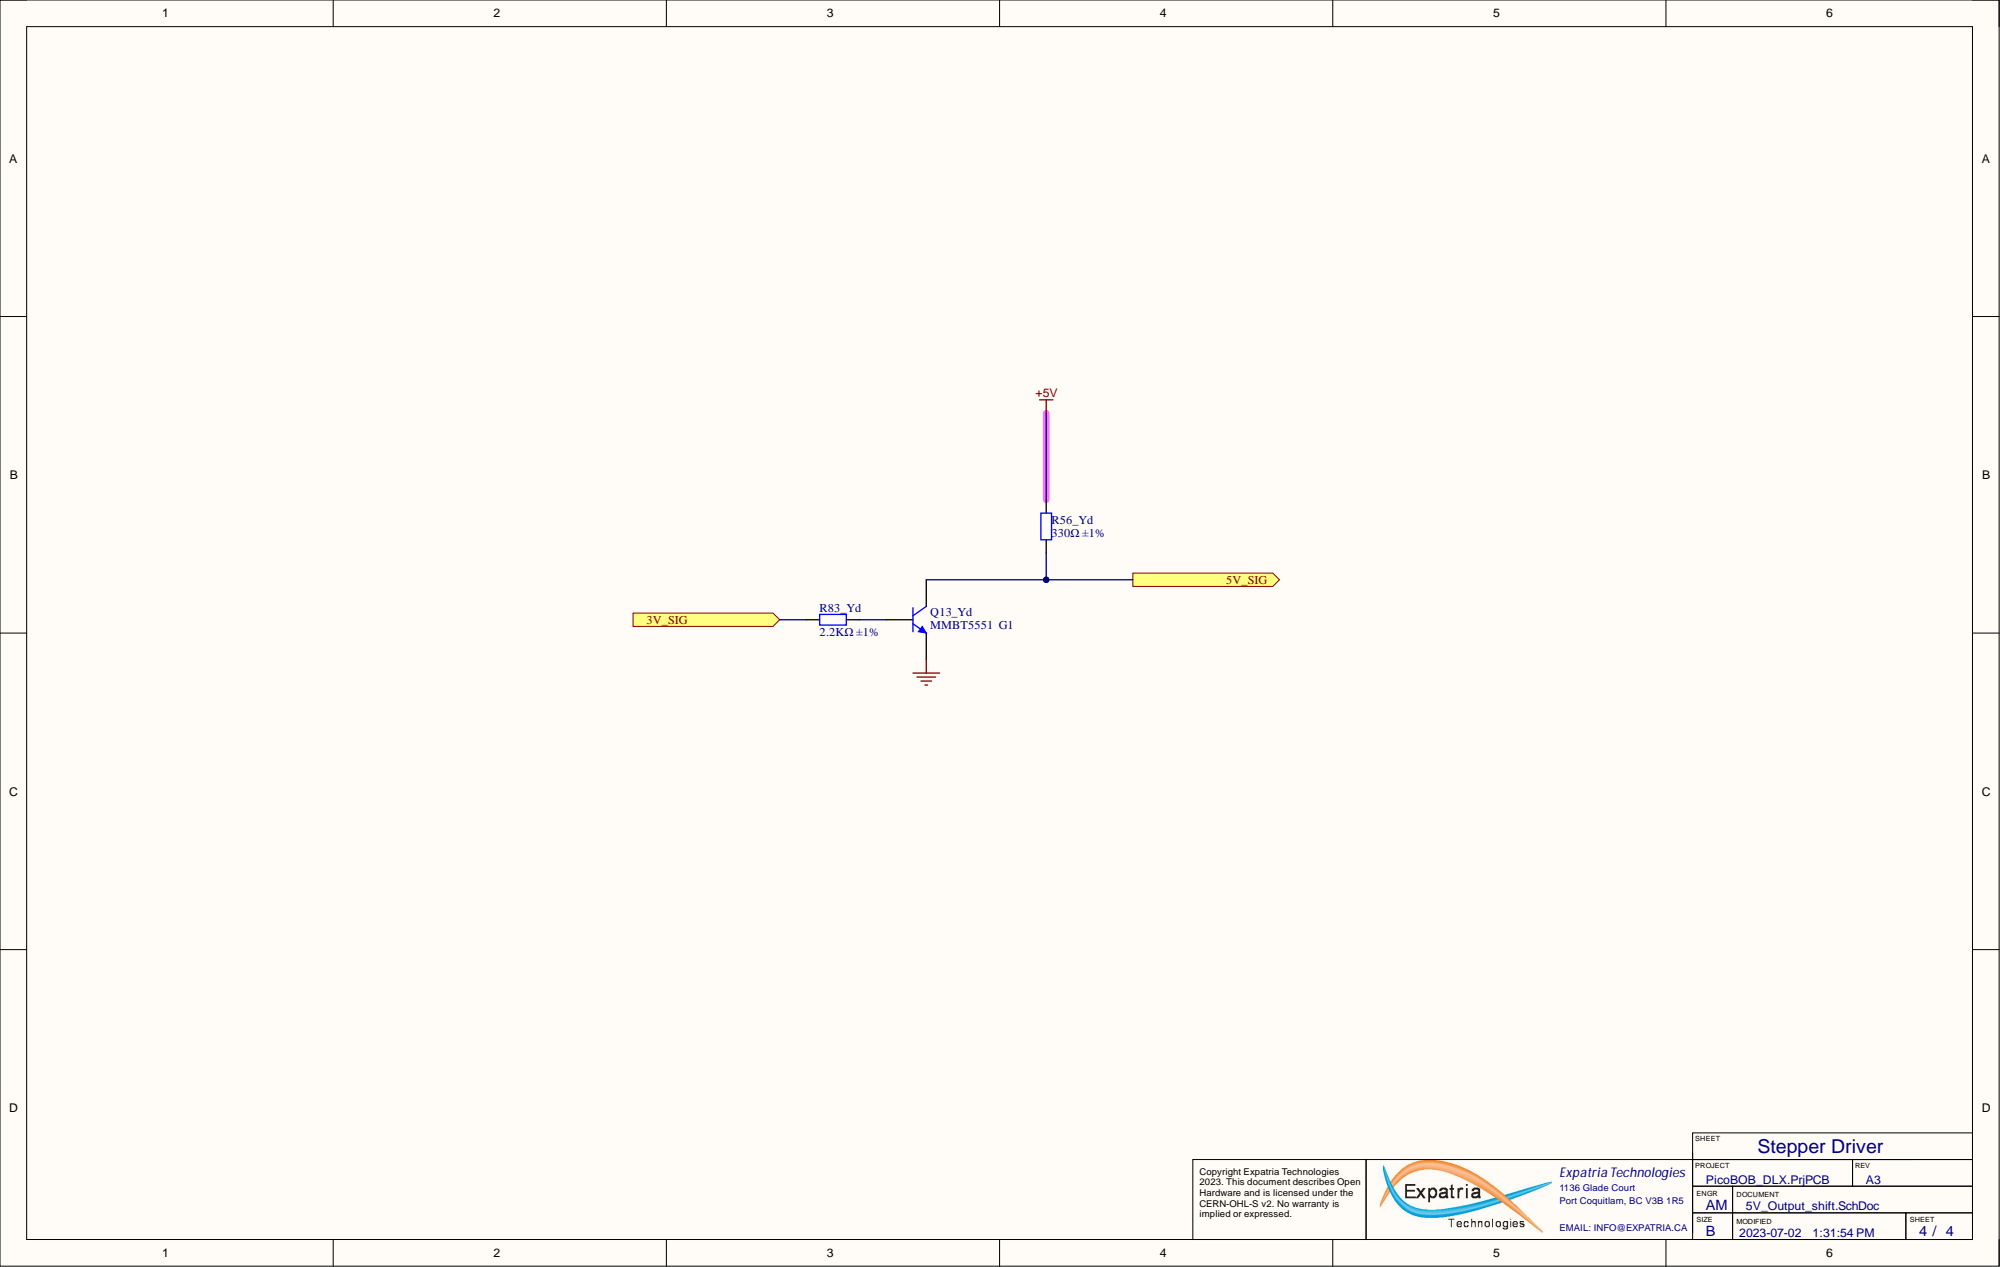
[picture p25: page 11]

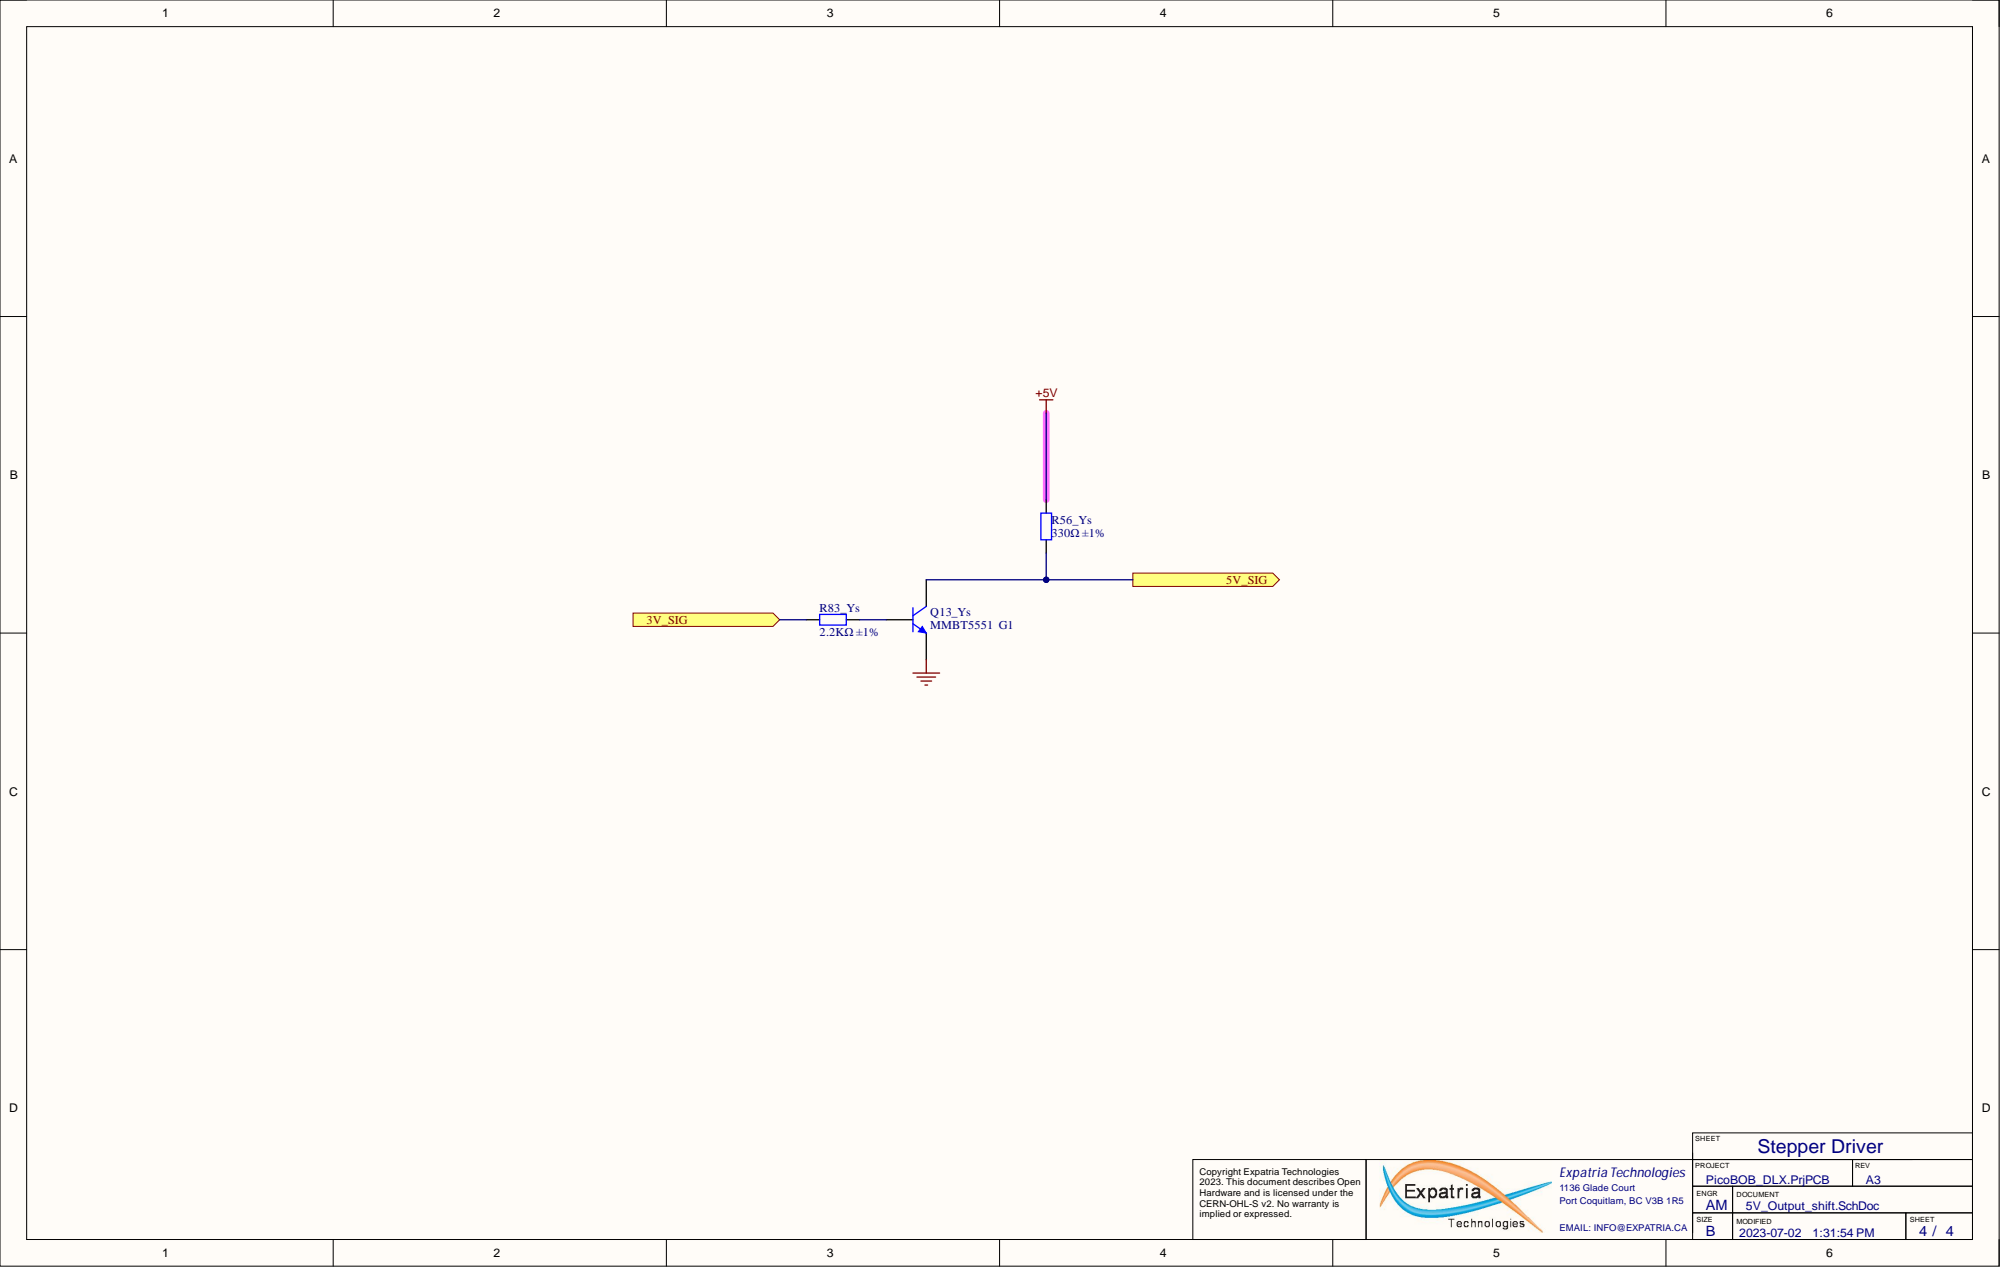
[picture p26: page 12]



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

ENGR AM | DOCUMENT I2C_Keypad.SchDoc

SIZE | MODIFIED 2023-07-02 1:31:54 PM | SHEET 12/ 14

EMAIL: INFO@EXPATRIA.CA
